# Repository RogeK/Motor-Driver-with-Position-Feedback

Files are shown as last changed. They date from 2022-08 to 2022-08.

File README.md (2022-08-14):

# Motor-Driver-with-Position-Feedback
This repo contains a design for a motor driver with position feedback HAT that can be attached to the 40 GPIO pins of the Pi. It is intended to be used to track and control the instantaneous position of the M1N10FB11G Brushless DC Motor which has an incremental encoder attached to its shaft. The scenarios that the daughter board with a Pi are used in include solar tracking systems, automatic sliding gate and a hybrid engine fan.

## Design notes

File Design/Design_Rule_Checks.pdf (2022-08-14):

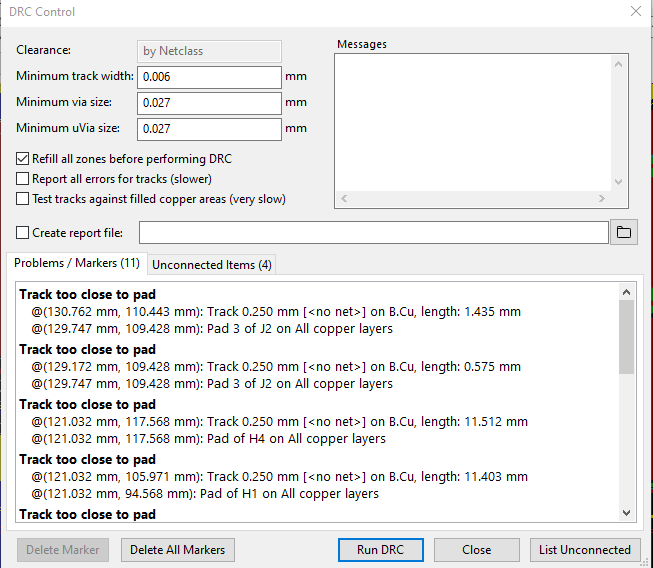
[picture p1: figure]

Screen Shot of the DRC configuration window

The final design does not pass all the tests. The components chosen were too large for the constrained area of the board that we were working with. The components were therefore too close to each other making the tracks to form a gridlock. As a result, not all components were connected.

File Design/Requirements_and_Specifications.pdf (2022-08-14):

# Requirements

# Scenario1 – Hybrid engine fan

- R1.1: Device physically be a microPI HAT.
- R1.2: Device be small in size.
- R1.3: Can be attached to the 40 GPIO pins of the Pi.
- R1.4: Possible to track the instantaneous position of a Brushless DC Motor.
- R1.5: The instructions written on the Pi will be executed by this daughter board.

### - R1.6: User should be able to connect the board directly to the mains - R1.7: Support multiple applications & allow them to work with any standard Pi - R1.8: Should have status LEDs to give feedback when the board has been powered and when the motor is running

- R1.9: Device be protected from overheating, dust and moisture.
- R1.10: Device provides audible feedback.

# Scenario 2 - Linear actuator for solar tracking systems (solar tracker)

- R2.1: Device physically be a microPI HAT.

### - R2.2: Device be small in size. (Should not be larger than the Pi)

- R2.3: Can be attached to the 40 GPIO pins of the Pi.
- R2.4: Possible to track the instantaneous position of a Brushless DC Motor.
- R2.5: The instructions written on the Pi will be executed by this daughter board.

### - R2.6: User should be able to connect the board directly to the mains - R2.7: Support multiple applications & allow them to work with any standard Pi ●

R2.8: Should have status LEDs that connects to the motor IC and power circuitry.
- R2.9: Device be protected from overheating, dust and moisture.
- R2.10: Device is capable of operating over multiple days in the dessert.

# Scenario 3 – Automatic sliding gate

- R3.1: Device physically be a microPI HAT.

- R3.2: Device be small in size.
- R3.3: Can be attached to the 40 GPIO pins of the Pi.
- R3.4: Possible to track the instantaneous position of a Brushless DC Motor.
- R3.5: The instructions written on the Pi will be executed by this daughter board.
- R3.6: Power supply circuitry board for motor and driver IC.
- R3.7: Support multiple applications & allow them to work with any standard Pi.
- R3.8: Should have status LEDs that connects to the motor IC and power circuitry.
- R3.9: Device be protected from overheating, dust and moisture.
- R3.10: Device provides audible feedback.
- R3.11: Device is capable of operating over multiple days in the dessert.

# Specifications

# Mechanical Specifications

Requirement | Specification(s) | Acceptance Test Criteria
R1.1: Device be small in size | S1.1: Have a small mechanical form factor (65mm by 30.5mm) S1.2: Weight limited to 15g | Final design weight is within limits.
R1.2: Should be possible to physically attach the board to Pi-Zero | S1.3: Should have 4 mounting holes that are adjacent to the mounting holes of the Pi | Mounting holes should have a diameter of 2.75mm
R1.4: The board should function normally in a dusty and moist environment | S1.4: Fittable to a MX410 Mesh-G RGB casing S1.5: As dust may cause poor contact of the pins from the encoder, use a screw terminal to connect the encoder pins the board S1.6: Have an NTC near the pins to protect the board from arcing | Final design fitted in specified fitting and products be AEC-Q100 qualified. The screw terminal should be made of a material that does not foul
R1.5: Should be possible for a non-technical staff to know when the board is faulty | S1.7: Board should have well labelled led indicators to show when board is on and when board is running | LED indicating the powering of the board should be near the power supply, should be red in colour LED indicating that the motor is running should be near the motor connection pins and should be green in colour.

# Electrical Specification

Requirement | Specification(s) | Acceptance Test Criteria
R1.4, R2.4 & R3.4 Possible to track the instantaneous position of a Brushless DC Motor. | S1.9: Board should connect to the pins of the incremental encoder. Should be capable of receiving input from the encoder and send it to the Pi for processing. Should also be capable of receiving position control instructions from the Pi and executing it on the motoe | Track position of the motor. Signal output within the 0-3.3V required range
R1.6, R2.6 & R3.6: The Hat should not be dependent on the Pi for its power requirements | S1.6, S2.6 & S3.6: The board be powered by the mains through a 5mm Barrel Jack -Should have power supply circuitry board for motor and driver IC. -PSU should have an SMPS regulator, preferably an IC(eg LTC3638) -Vin = 12V from a Barrel Jack -Vout = 5V 2.5A to control the DC motor | The Hat is power independent
R1.7, R2.7 & R3.7 Support multiple applications & allow them to work with any standard Pi | S1.7 Temperature & position sensors, Current and voltage sensing, Safety & glue logic and wired interface. S2.7 Feedback position sensor, timer, sun detector sensors, Relays and limit switch. S3.8 Feedback position TR sensor, motion detector sensors, Relays and limit switch. | Interface with position sensors, limit switches, TR sensors, relays and power supplies.
R2.10 & 3.11 Device is capable of operating over multiple days in the dessert | S2.10 & S3.11 Operating Temperature Range of -40 to 50C | All components selected are rated for operation within given range Final design is chamber tested for 10hrs operation at -40, 0, and 50C
All: Should be possible to add other boards on top of the motor driver board that will also make use of the functionalities of the Pi | Should have 40 header pins adjacent to the 40 GPIO pins of the Pi | The other Pi GPIO pins not being used by the board should still be usable
All: The Pi should be protected from any spikes from the hat | S1.3: A ZVD circuit should be used to guard the inputs to the pi from the encoder | There should be a ZVD circuit for every Pi input from the Hat

# Functional Specifications

Requirement | Specification(s) | Acceptance Test Criteria
R1.8, R2.8 & R 3.8: Should have status LEDs that connects to the motor IC and power circuitry. | S1.8 Warning LED red display when faulty and green for health operation of fan. S2.8 LEDs green when in operation visible over 5m S3.8 LEDs green when opening and red when closed, visible over 5m | Status LEDs indicate motor power, motor direction, motor connected/not, high current draw warning. Pass SANSB compliance test AB789
R1.10 & R3.10 Device provides audible feedback | S1.10 Feedback must be audible for faulty fan. S3.10 Feedback must be audible over 20m during operation. | Pass SANSB audio compliance test AB789

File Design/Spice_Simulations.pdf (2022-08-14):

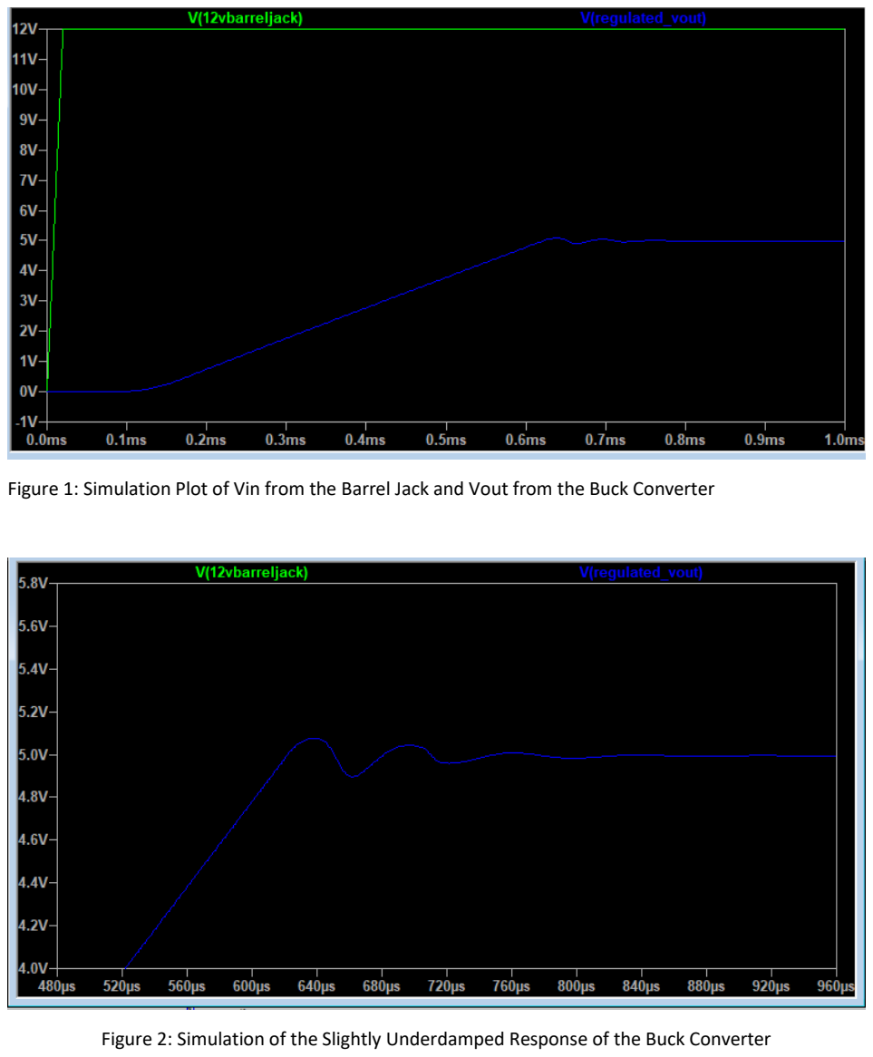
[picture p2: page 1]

Figure 1: Simulation Plot of Vin from the Barrel Jack and Vout from the Buck Converter

Figure 2: Simulation of the Slightly Underdamped Response of the Buck Converter

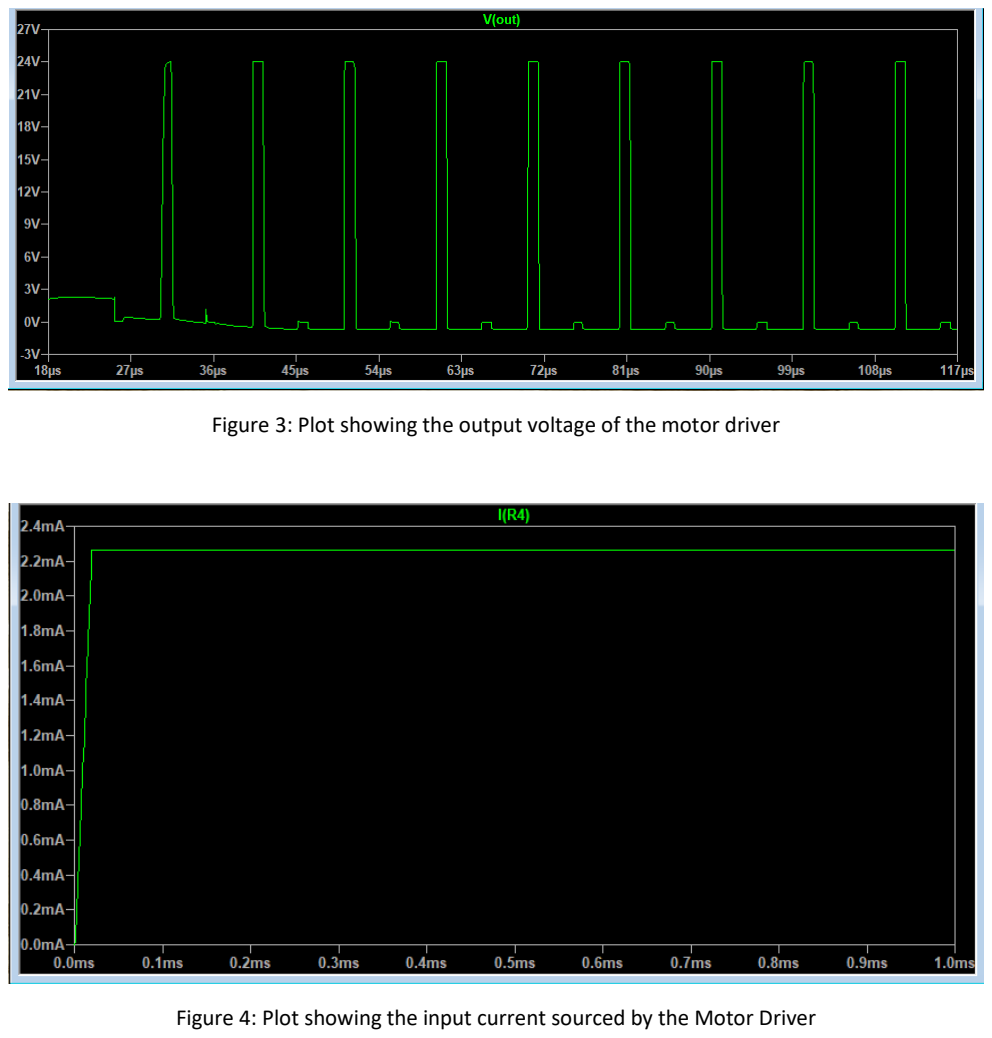
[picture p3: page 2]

Figure 3: Plot showing the output voltage of the motor driver

Figure 4: Plot showing the input current sourced by the Motor Driver

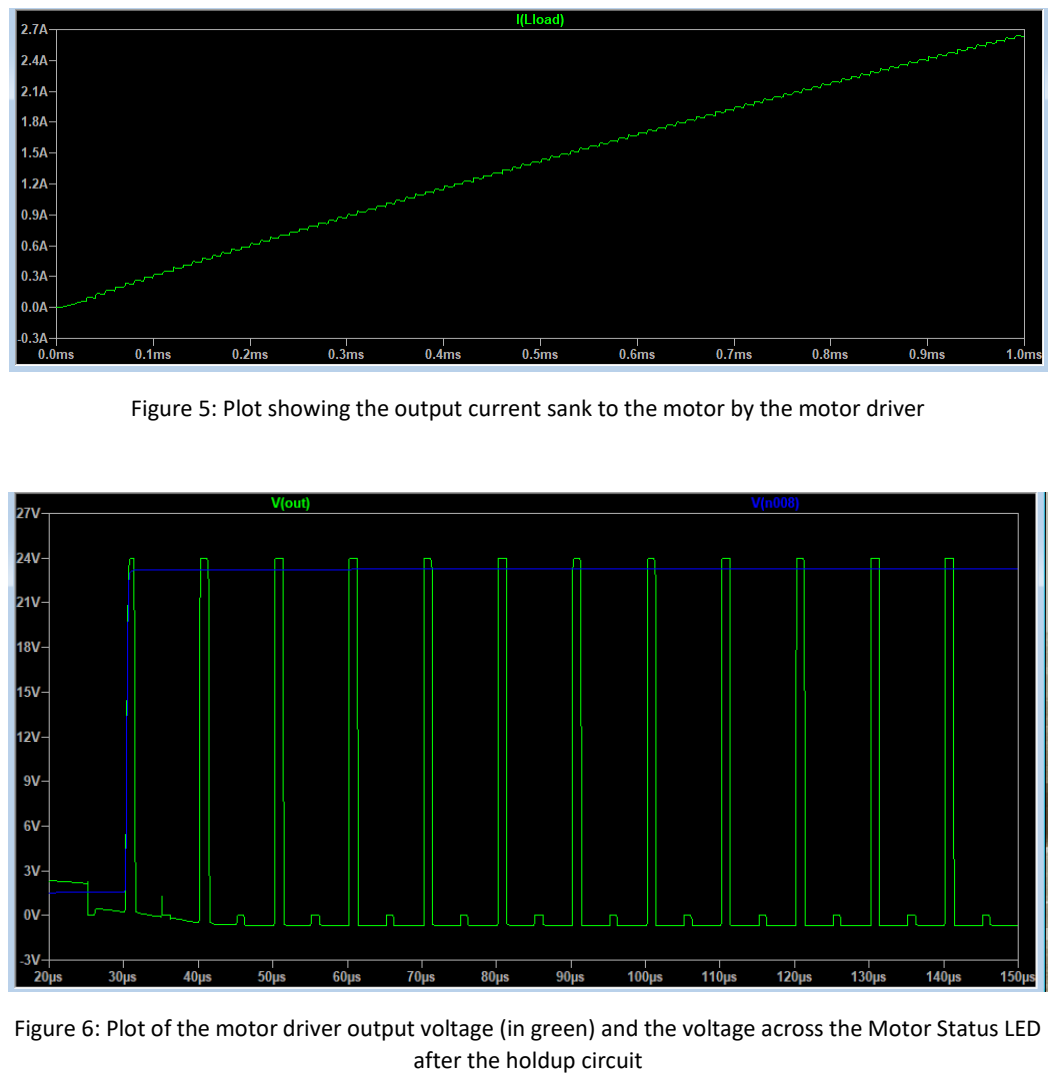
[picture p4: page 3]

Figure 5: Plot showing the output current sank to the motor by the motor driver

Figure 6: Plot of the motor driver output voltage (in green) and the voltage across the Motor Status LED after the holdup circuit

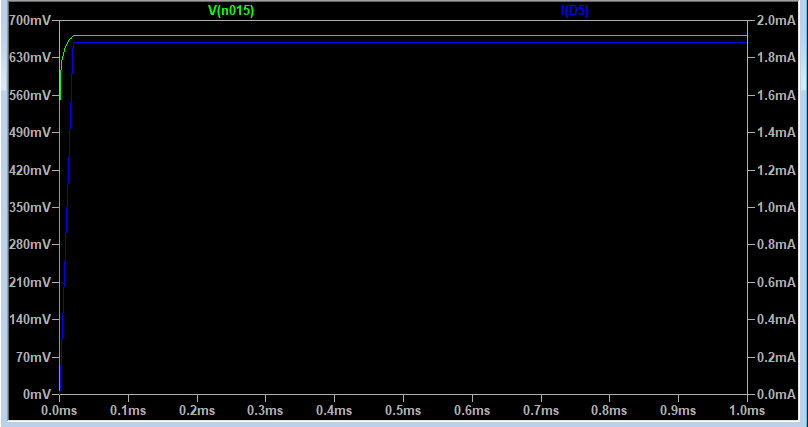
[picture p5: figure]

Figure 7: Voltage Across (Green) and Current through (Blue) the Power Supply Status LED

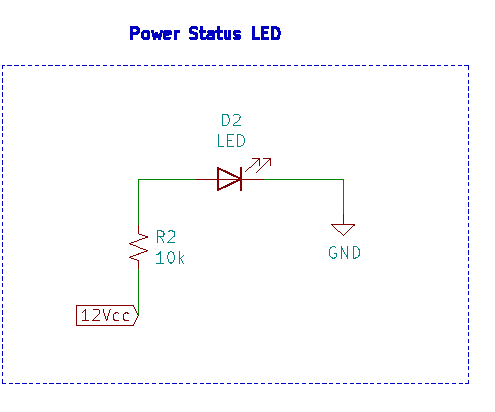
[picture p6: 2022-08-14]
Status LEDs Submodule/Power_Status_LED_schematic.png

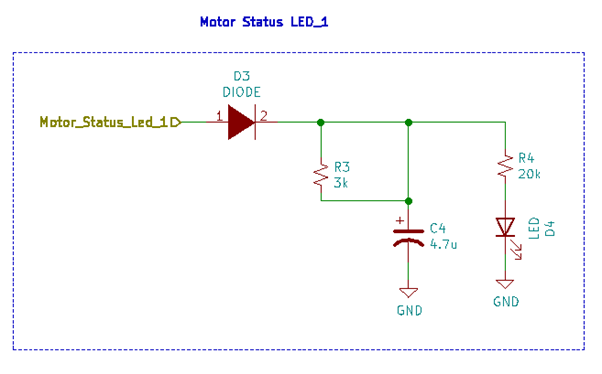
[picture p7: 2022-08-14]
Status LEDs Submodule/Motor_Status_LED1_Schematic.png

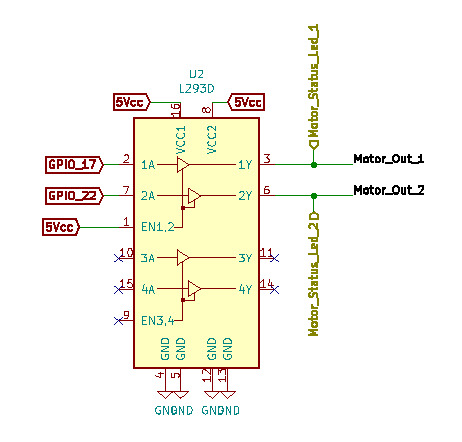
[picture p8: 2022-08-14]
Amplifier Submodule/Amplifier_Schematic.png

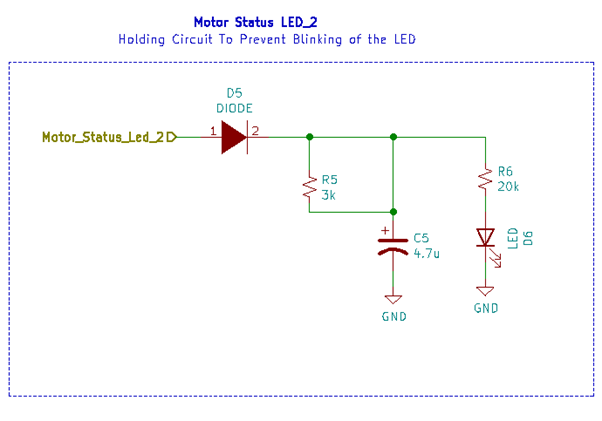
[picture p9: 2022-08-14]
Status LEDs Submodule/Motor_Status_LED2_Schematic.png

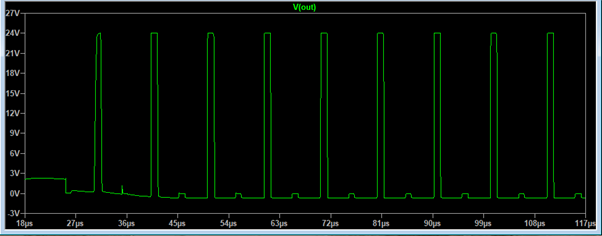
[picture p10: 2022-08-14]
Amplifier Submodule/Amplifier_Simulation.png

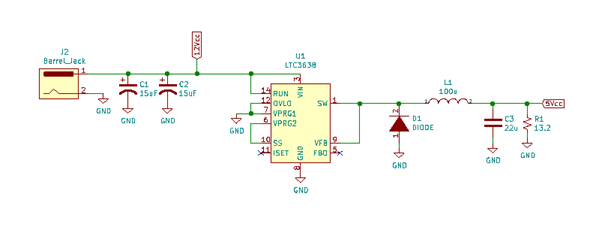
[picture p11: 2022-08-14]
Power Supply Submodule/Power_Supply_shematic.png

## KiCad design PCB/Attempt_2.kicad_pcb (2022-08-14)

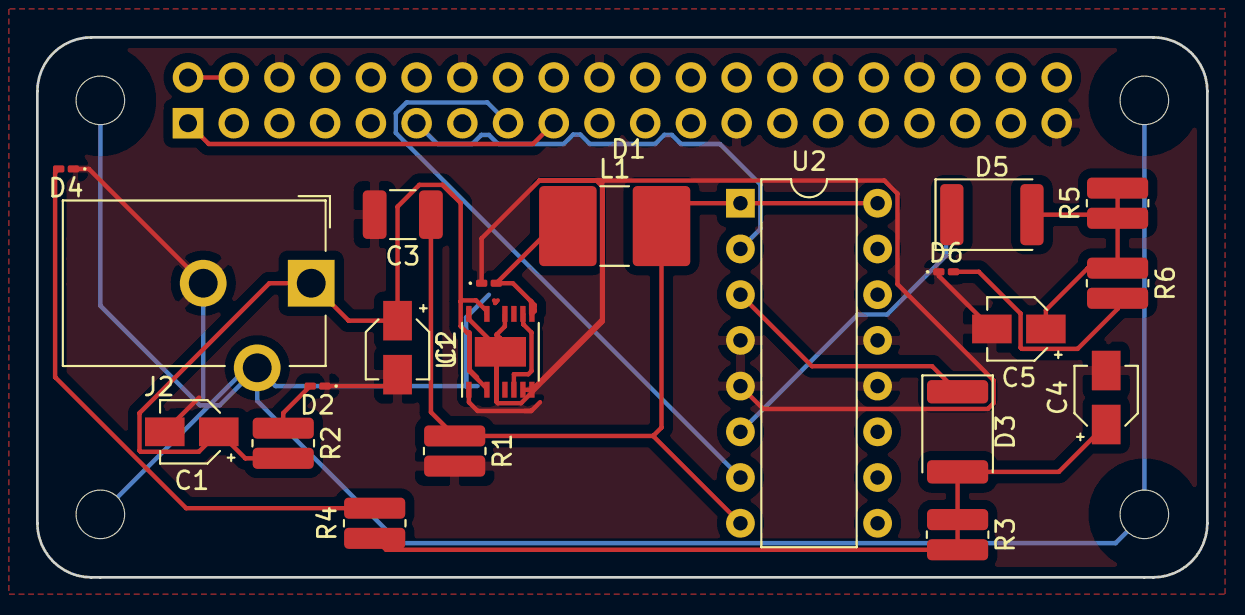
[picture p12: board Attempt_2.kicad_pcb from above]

Board: 2 copper layers, 65.0 x 30.0 mm, 26 parts (1 on the bottom side), 16 nets.

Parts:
C1, C2: 15uF; CP_Elec_3x5.3
C3: 22u; C_1210_3225Metric_Pad1.33x2.70mm_HandSolder
C4, C5: 4.7u; CP_Elec_3x5.3
D1: DIODE; D_0201_0603Metric_Pad0.64x0.40mm_HandSolder
D2, D4, D6: LED; LED_0201_0603Metric_Pad0.64x0.40mm_HandSolder
D3, D5: DIODE; D_1812_4532Metric_Pad1.30x3.40mm_HandSolder
H1, H2, H3, H4: MountingHole; MountingHole_2.7mm_M2.5_uHAT_RPi
J1: GPIO_CONNECTOR; PinSocket_2x20_P2.54mm_Vertical_Centered_Anchor
J2: Barrel_Jack; BarrelJack_CUI_PJ-102AH_Horizontal
L1: 100u; L_2816_7142Metric_Pad3.20x4.45mm_HandSolder
R1: 13.2; R_0612_1632Metric_Pad1.18x3.40mm_HandSolder
R2: 10k; R_0612_1632Metric_Pad1.18x3.40mm_HandSolder
R3, R5: 3k; R_0612_1632Metric_Pad1.18x3.40mm_HandSolder
R4, R6: 20k; R_0612_1632Metric_Pad1.18x3.40mm_HandSolder
U1: LTC3638; Linear_MSOP-12-16-1EP_3x4mm_P0.5mm
U2: L293D; DIP-16_W7.62mm

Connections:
5Vcc: C3.1, L1.2, R1.1, U2.1, U2.8, U2.16
12Vcc: C1.1, C2.1, J2.1, R2.2, U1.3, U1.14
+3V3: J1.1, J1.17
+5V: J1.2, J1.4
/Led_Status/Motor_Status_Led_1: D3.1, U2.3
/Led_Status/Motor_Status_Led_2: D5.1, U2.6
GND: C1.2, C2.2, C3.2, C4.2, C5.2, D1.1, D2.1, D4.1, D6.1, J1.6, J1.9, J1.14, J1.20, J1.25, J1.30, J1.34, J1.39, J2.2, R1.2, U1.7, U1.8, U1.12, U1.16, U1.17, U2.4, U2.5, U2.12, U2.13
GPIO_17: J1.11, U2.2
GPIO_22: J1.15, U2.7
unnamed: C4.1, D3.2, R3.1, R3.2, R4.1
unnamed: C5.1, D5.2, R5.1, R5.2, R6.1
unnamed: D1.2, L1.1, U1.1, U1.9
unnamed: D2.2, R2.1
unnamed: D4.2, R4.2
unnamed: D6.2, R6.2
unnamed: U1.6, U1.10

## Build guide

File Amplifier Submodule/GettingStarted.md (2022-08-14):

1. The Motor Position Feedback Subsystem is made up of the incremental encoder, the motor driver L293D and the Pi  

2. The motor driver L293D acts as our amplifier. It sinks 250mA from the Power Supply and amplifies it to 2A  

3. The incremental encoder will be connected to the shaft of the DC motor M1N10FB11G.It will however be controlled by the board through its pins.  

4. The encoder has 6 pins that will be connected to the PiHat through screw terminals instead of header pins which may not work well in a dusty environment.  

5. The pins of the encoder are as follows:

| PIN | Description |
| --- | --- |
| Q1 | Supplies current into/out of the motor from the motor driver. Receives instructions from the Pi through the motor driver. The status LED 2 is connected to this pin to indicate when the motor is running |
| Q2 | Supplies current into/out of the motor from the motor driver. Receives instructions from the Pi through the motor driver. The status LED 3 is connected to this pin to indicate when the motor is running |
| Vcc | Powers the encoder. |
| GND | Ground Pin |
| Digital Pin 1 | Sends feedback to the Pi regarding the motors position and direction. |
| Digital Pin 2 | Sends feedback to the Pi regarding the motors position and direction. |

6. Pins Q1 and Q2 from the encoder will be connected to the output of the motor driver L293D which will serve to amplify the low current from the voltage regulator to a high enough current that can drive the motor  

7. The L293D was also chosen because of its high-Noise-Immunity Inputs protecting the subsystem against noise that may come from the power supply and from the inrush current it may experience when the motor turns on  

8. The pins of the L293D are as follows:

| PIN | Description |
| --- | --- |
| 1 | Enable pi. When this pin is powered, it enables pins 1 and 2. |
| 2 | Receives input from the Pi through GPIO4 of the Pi which is accessible through the header pins. |  
| 3 | This is the output pin of pin 2. Offers path for bidirectional current to and from the motor. |
| 6 | This is the output to pin 3. Offers path for bidirectional current to and from the motor. |
| 7 | Receives input from the Pi through GPIO3 of the Pi which is accessible through the header pins. |

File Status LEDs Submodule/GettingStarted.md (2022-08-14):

**Status LEDs**

There are 3 status LEDs, one is positioned near the jack and turns on to indicate that the PiHat is connected to the mains. The second and third LEDs are connected on the output pins Q1 and Q2 of the motor driver through a hold up circuit. These two LEDS turn on to indicate that the motor is running. Since the output of the motor driver is a PWM signal, the LEDS were found to be increasing and decreasing in brightness depending on the duty cycle. To prevent this, a hold up circuit was placed between the led and the motor driver.

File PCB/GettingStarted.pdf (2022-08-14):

STARTING, USING AND SWITCHING OFF THE BOARD

Components needed

i) Motor Control Board
ii) | Pi-Zero
iii) | DC Motor
iv) | Rotary Encoder

Powering the Device

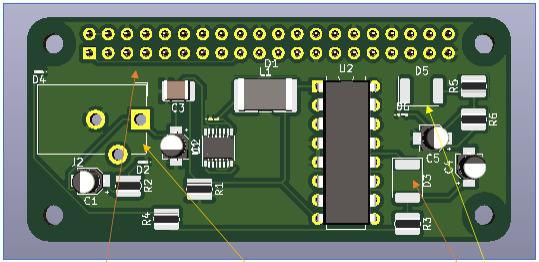
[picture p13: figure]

Figure 1: Motor Control Board

Powering the Motor Control Board

Solder a female Barrel Jack to the board. The terminals of the Barrel Jack should be soldered to the exposed copper near the writings J2 on the board. Connect the board to through a male Barrel Jack. The Diode D1 should light up when the board is correctly powered.

Alternatively, you can solder positive and negative rails to the J2 terminals. The board has reverse voltage protection and therefore will not be broken if the negative terminal is connected to the positive terminal. If the diode D1 does not go on, invert your connection

Connecting the board to the Pi

The board is connected to the Pi through the 40 GPIO pins on the board. This pins will fit perfectly on the pi pins.

*Note: GPIO_17 and GPIO_22 of the board are NOT connected to the Pi

Connecting the Board to the Motor

Solder LEDS D5 and D3
here Solder Barrel Jack
Here

Solder LED Diodes D5 and D3 to the board. You are free to choose the colors of your choice. These LEDs light up to indicate that the motor is running

Connect the V+ and V- pins of the motor to the motor control board through GPIO_17 and GPIO_22 respectively. These two pins are connected to the Pi and therefore the large current they carry will not damage the Pi.

Connecting the Board to the Rotary Encoder

Connect the encoder to the board through GPIO_12 and GPIO_13. This acts as the feedback channel

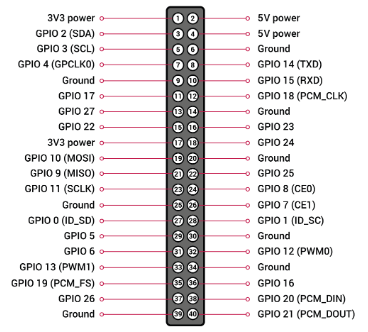
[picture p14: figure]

Figure 2: GPIO Pin Layout

Switching off the Board

Stop the motor then unplug the power plug from the Barrel Jack

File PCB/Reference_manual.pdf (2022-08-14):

# Technical Reference Manual DC Motor Position Control With Feedback

## MbuyiTinoRoge Electronics Company Limited

Date | : | 10 June 2021
Revision | : | 07
Prepared by | : | Eric Mbuyiswa, Tinotenda Magora, King’oo Njoroge
| | Mthmbu004,mgrtin001,njrkin001

## 1. Introduction

### 1.1. Document Identification

This document describes the design and use of the DC Motor Position Control with Feedback board.

### 1.2. System Overview

The board can be used together with a Pi to control the position of a DC motor and receive

feedback.

### 1.3. Reference Documents

The present document is prepared on the basis of the following reference documents, and should be read in conjunction with them.

—. LTC3638 Datasheet. (https://www.analog.com/en/products/ltc3638.html)
—. L293D Datasheet(https://www.ti.com/lit/ds/symlink/l293.pdf)

## 2. System Description

This section is intended to give a general overview of the basis for the DC motor control system design, of its division into hardware and software modules, and of its development and implementation.

### 2.1. Introduction

Position feedback is essential when designing and operating a robot. This is possible using Servo Motors. Servo Motors are expensive to purchase and require complex coding to control. This board enables the use of any affordable DC motor as a servo motor.

### 2.2. System Requirements

The operational scenarios considered place certain requirements on the whole something system, and on the modules that comprise it.

### 2.3. Module Design

The board is divided into 3 submodules,

i) Power Supply Unit
ii) | Led Status LED
iii) | Amplifier

## 3. Hardware Design

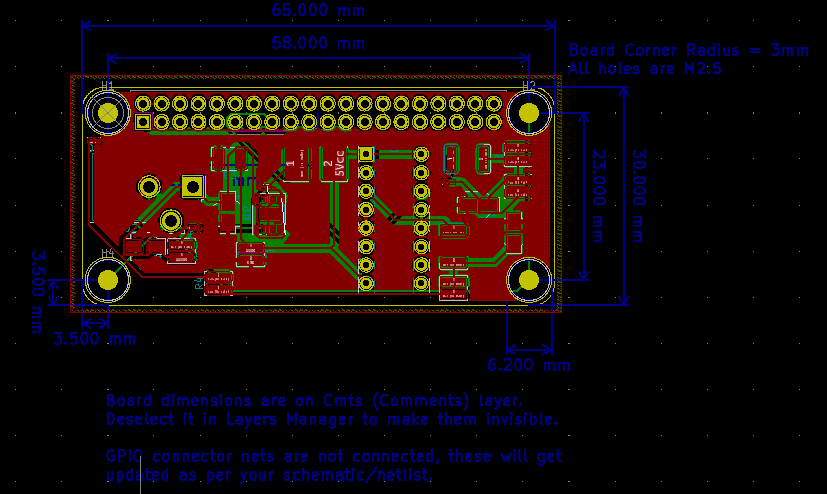
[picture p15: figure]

Figure 1: Dimensions of the piHat

The board is 65mm by 30mm wide

### 3.1. Hardware Design

### 3.1.1. Power Supply

A female Barrel Jack should be soldered to the board.

The board is powered by +12VDC through this Barrel Jack

An LED should turn on to indicate that the board is powered

### 3.1.2. Amplifier(Motor Driver)

The motor driver drives the motor.

Solder diodes D1 and D5 of the colour of your choice on the board. This diodes will turn on to indicate that the motor is running.

## 4. Software Design

This board will execute code written on the Pi

## 5. Safety Implications

The board should not be in contact with water.
The board may heat up if the motor runs for a long time

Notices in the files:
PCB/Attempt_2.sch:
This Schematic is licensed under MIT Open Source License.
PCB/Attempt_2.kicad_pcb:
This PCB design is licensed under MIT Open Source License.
